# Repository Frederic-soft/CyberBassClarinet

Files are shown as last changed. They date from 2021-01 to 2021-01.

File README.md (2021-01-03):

Cyber bass clarinet
=====================
I had temporary issues in my left pinky during a few months in 2020 and could no longer push the low-D and G sharp/D sharp keys on my bass clarinet.

I transformed the tip of the keys into capacitive touchpads to be sensed by an ESP32 development board, which in turn drives a servo-motor to pull the keys.

Contents
--------
* The ```Micropython``` folder contains the [Micropython](https://micropython.org/) code used to program the ICQUANZX Mini32 v1.3 development board I used.

* The openscad folder contains the [OpenScad](https://www.openscad.org/) source code of the block that holds the servo-motor on the upper clarinet body, as well as the rendered STL file that you can use to print this piece.

* The MP4 file shows how the system works.

How to build yours
------------------
The ESP32 and its 1000mAh 3.7V lithium battery are wrapped in black tape and stuck to the clarinet body using double-sided tape.

The 3D-printed servo-motor support is also stuck using double-sided tape.

I tried different solutions to link the servo-motor and the keys.
The best one seems to be to use soft brass wire, as found on Champagne bottles to secure the cork.
Fishing wire will break early and may get tangled.

To carry your bass clarinet in its case, switch the ESP32 off, remove the servor motor from its support.
The ESP32, the servo-motor and all the wiring stay with the lower body.
The upper body only has the 3D-printed support.

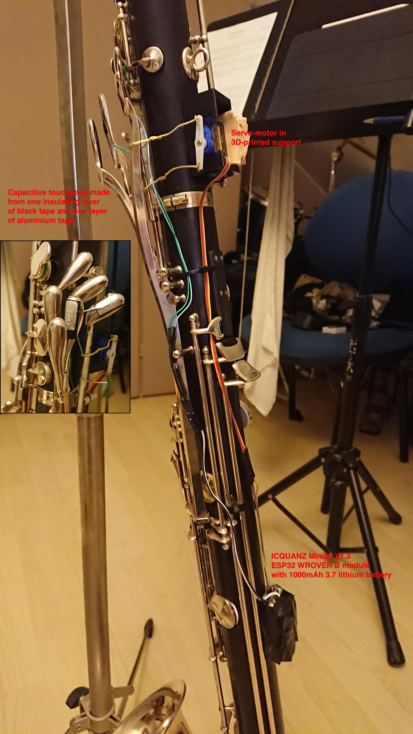
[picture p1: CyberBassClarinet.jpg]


© Frédéric Boulanger frederic.softdev@gmail.com  
2019-08-28  
This software is licensed under the Eclipse Public License 2.0

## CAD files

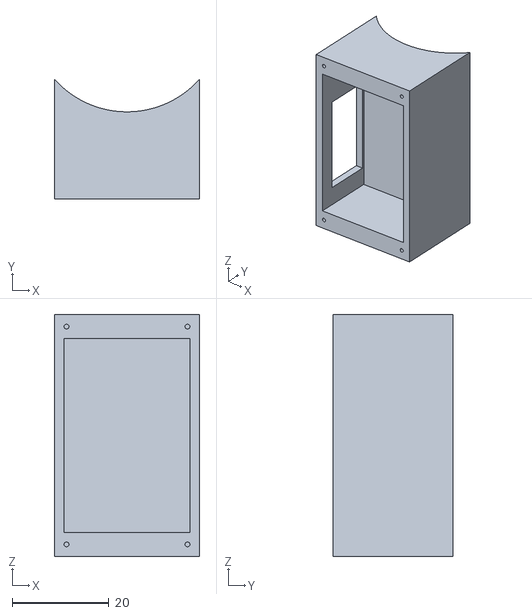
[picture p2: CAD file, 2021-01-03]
openscad/mainblock-servo.stl
30.0 x 24.8 x 50.0

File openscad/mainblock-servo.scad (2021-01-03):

difference () {
  cube(size=[30, 25, 50]);
  translate([2,-1,5]) cube(size=[26, 18, 40]);  // hollow cube
  translate([15, 38, -1]) cylinder(h=93, r=20, $fn=200);  // clarinet body
  translate([-7, 4, 10]) cube(size=[22, 12.5, 25]);  // servo
  translate([2.5, 4.9, 2.5]) rotate([90,0,0]) cylinder(h=5, r=0.5, $fn=100);
  translate([27.5, 4.9, 2.5]) rotate([90,0,0]) cylinder(h=5, r=0.5, $fn=100);
  translate([27.5, 4.9, 47.5]) rotate([90,0,0]) cylinder(h=5, r=0.5, $fn=100);
  translate([2.5, 4.9, 47.5]) rotate([90,0,0]) cylinder(h=5, r=0.5, $fn=100);
};

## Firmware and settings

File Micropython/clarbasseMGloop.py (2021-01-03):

import machine
import time
import esp32
import sys

# rest angle
rest = 70
# low D angle (pad 1)
lowD = 100
# c# angle (pad 2)
csharp = 40

# capa threshold
cthres = 260

tp1 = machine.TouchPad(machine.Pin(33))
tp1.config(cthres)
tp2 = machine.TouchPad(machine.Pin(14))
tp2.config(cthres)
# esp32.wake_on_touch(True)
servo = machine.PWM(machine.Pin(21))
servo.freq(50)
servo.duty(rest)
# time.sleep_ms(150)
tp = None
# 32 = +90°
# 81 = 0°
# 128 = -90°
# Stop if pin 5 is grounded (allows pyrshell to take control over the board)
stop = machine.Pin(5, machine.Pin.IN, machine.Pin.PULL_UP)
if stop.value() == 0 :
  print("Pin 5 is grounded, stopping.")
  sys.exit(0)

while True :
#  print("Going to sleep")
#  machine.lightsleep()
#  print("Waking up")
  while not (tp1.read() < cthres or tp2.read() < cthres) :
    time.sleep_ms(50)

  if tp1.read() < cthres :
#    print("Pad 1 touched")
    tp = tp1
    servo.duty(lowD)
  else:
#    print("Pad 2 touched")
    tp = tp2
    servo.duty(csharp)
  
  while tp.read() < cthres :
    time.sleep_ms(50)
#  print("Pad released")
  servo.duty(rest)
  time.sleep_ms(50)

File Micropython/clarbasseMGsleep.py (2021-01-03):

import machine
import time
import esp32

tp1 = machine.TouchPad(machine.Pin(33))
tp1.config(300)
tp2 = machine.TouchPad(machine.Pin(14))
tp2.config(300)
esp32.wake_on_touch(True)
servo = machine.PWM(machine.Pin(21))
servo.freq(50)
servo.duty(74)
time.sleep_ms(150)
tp = None
# 32 = +90°
# 81 = 0°
# 128 = -90°
while True :
  print("Going to sleep")
  machine.lightsleep()
  print("Waking up")
  if tp1.read() < 300 :
    tp = tp1
    servo.duty(119)
  else:
    tp = tp2
    servo.duty(32)
  
  while tp.read() < 300 :
    time.sleep_ms(10)
  print("Pad released")
  servo.duty(74)
  time.sleep_ms(150)
  # if tp.read() < 300 :
  #   servo.duty(119)
  # else :
  #   servo.duty(74)
  # time.sleep_ms(100)

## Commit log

2021-01-03 Initial commit.
    [mainblock-servo.scad, mainblock-servo.stl]
2021-01-03 Added instructions to carry the clarinet in its case.
